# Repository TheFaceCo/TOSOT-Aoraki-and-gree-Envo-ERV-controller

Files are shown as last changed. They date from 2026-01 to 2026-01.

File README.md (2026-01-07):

# TOSOT Aoraki and gree Envo ERV controller
This is a control board for the ductless minisplit ERV manufactured by Gree and sold under the TOSOT brand on amazon et al. It uses an ESP32-S3 WROOM1 microcontroller. 

The ERV is provided with 12V from the minisplit (unknown if this is enabled by default) and accepts PWM speed control. 12V is applied via the 2pin female header. I believe the OEM harness can be jammed onto this header. The ERV pulls about 10W at full speed. 

The motor expects 5V amplitude PWM, so the board includes a small amplifier to step the ESP 3.3v output up to 5v. The PWM output pin is attached to **GPIO1**

There is a standard 0.100" pitch pin header provided for the motor connector. The pitch isn't quite wide enough, but it works. A slightly wider pitch would be better. 

There is a 600mA switching regulator circuit to bring the incoming 12V down to 5v for the PWM, and a subsequent linear regulator to bring 5v down to 3.3v for the ESP32. I am not a SMPS designer, so this was generated using Texas Instruments WBENCH. Two of the ten initial PCB's blew up when power was applied, so this circuit should be considered mildly suspect. The generated assets are included in this repo. 600mA was chosen to allow for the power used by 2x particulate sensors and a CO2 sensor on the 5V rail.

There are two 5-pin JST ZH headers made available to connect Sensirion SPS30 particulate sensors, one for inside and one for outside. These devices are factory configured with identical I2C identifiers and therefore cannot share an I2C bus.  
The ESP32S3 can be configured with two I2C busses. These must be configured as follows:  
    **SDA1: GPIO48**  
    **SCL1: GPIO21**  
    **SDA2: GPIO13**  
    **SCL2: GPIO14**  

Bus #1 is attached to the connector nearest the BOOT and RESET buttons. Bus #2 is attached to the connector on the right-side flag below the power circuitry. 

The SPS30 uses the JST ZH conncetor as well, so a straight-through cable should work correctly. 

There is also a 6pin SH header provided for a Sensirion SCD30 CO2 sensor. This shares I2C bus #2. The SCD30 includes pullup resistors, and this may require that the external pullup resistors on the PCB be removed. This can be done by severing the two exposed traces on the bottom of the board, or by depopulating the two associated pullup resistors. The SCD30 includes a "ready" pin, which is attached to **GPIO12**

Also included is a 3pin JST SH header intended for a potentiometer if that's your preferred input device (If, for example, you intend to use it as a standalone device). 0/3.3V should be applied to the outer two pins, and the wiper should be connected to the center pin. The wiper is attached to **GPIO11**

There is a USB-C connector using the native ESP32 USB pins. This is intended for programming only. It will power the ESP, but not the ERV motor. I did not route the second pair of "B" data pins, so if it doesn't connect to a computer you may need to flip the USB connector. 

If you build firmware with the ESPHome tool in Home Assistant, the following stub should be included in the YAML:

```
fan:  
  - platform: speed  
    output: apartment_erv_fan_pwm  
    name: "Apartment ERV"  

output:  
  - platform: ledc  
    pin:  
      number: GPIO1  
      inverted: False  
      mode:   
        output: True  
        pullup: False  
    id: apartment_erv_fan_pwm  
    inverted: False  
    min_power: 0.20  
    zero_means_zero: True  
```

And the board type selected as follows:

```
esp32:  
  board: esp32-s3-devkitc-1  
  framework:  
    type: esp-idf  
```

PCBA

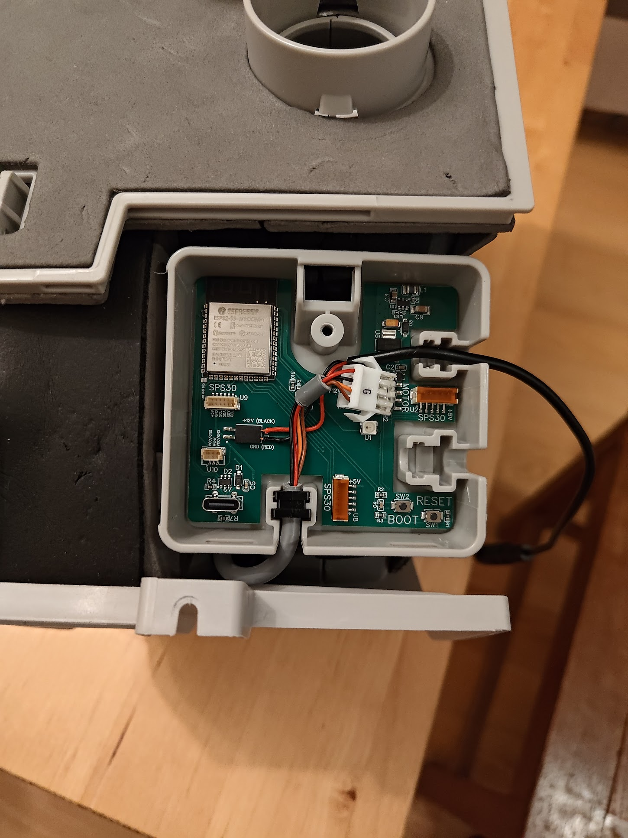
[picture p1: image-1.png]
installed


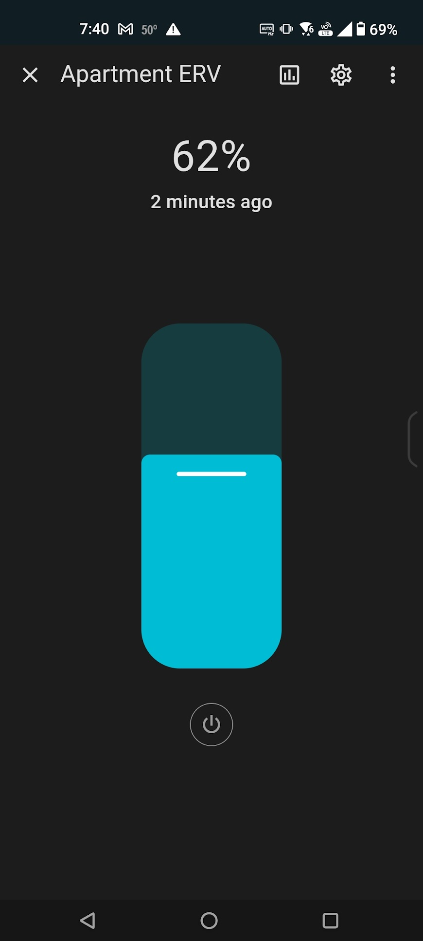
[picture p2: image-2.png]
homeassistant screenshot


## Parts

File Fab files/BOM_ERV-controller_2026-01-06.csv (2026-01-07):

ID | Name | Designator | Footprint | Quantity | Manufacturer Part | Manufacturer | Supplier | Supplier Part | Price | JLCPCB Part Class | link
1 | 10kΩ | R6,R12 | R0402 | 2 | 0402WGF1002TCE | UNI-ROYAL(厚声) | LCSC | C25744 | 0.001 | Basic Part | https://item.szlcsc.com/323315.html
2 | 10uF | C1 | CAP-SMD_L3.2-W1.6-RD-C7171 | 1 | TAJA106K016RNJ | Kyocera AVX | LCSC | C7171 | 0.116 | Basic Part | https://item.szlcsc.com/210648.html
3 | 100nF | C8 | C0402 | 1 | CL05B104KO5NNNC | SAMSUNG(三星) | LCSC | C1525 | 0.001 | Basic Part | https://item.szlcsc.com/15869.html
4 | 47uF | C9 | C1206 | 1 | CL31A476MPHNNNE | SAMSUNG(三星) | LCSC | C96123 | 0.071 | Basic Part | https://item.szlcsc.com/89171.html
5 | TS-1088-AR02016 | SW1,SW2 | SW-SMD_L3.9-W3.0-P4.45 | 2 | TS-1088-AR02016 | XUNPU(讯普) | LCSC | C720477 | 0.045 | Basic Part | https://item.szlcsc.com/457636.html
6 | 22uF | C3 | C0805 | 1 | CL21A226MAQNNNE | SAMSUNG(三星) | LCSC | C45783 | 0.024 | Basic Part | https://item.szlcsc.com/373011.html
7 | B5819W_C8598 | D1,D3 | SOD-123_L2.7-W1.6-LS3.7-RD-1 | 2 | B5819W SL | CJ(江苏长电/长晶) | LCSC | C8598 | 0.023 | Basic Part | https://atta.szlcsc.com/upload/public/pdf/source/20210423/C2828417_EF1BF8BE3D48F97E320B09B073C89160.pdf
8 | 4.7uH | L1 | L1008 | 1 | LQM2HPN4R7MG0L | muRata(村田) | LCSC | C82314 | 0.072 | Extended Part | https://item.szlcsc.com/77923.html
9 | 56.2kΩ | R11 | R0402 | 1 | RC0402FR-0756K2L | YAGEO(国巨) | LCSC | C183355 | 0.001 | Extended Part | https://item.szlcsc.com/323315.html
10 | TPS561208DDCR | U11 | TSOT-23-6_L2.9-W1.6-P0.95-LS2.8-BR | 1 | TPS561208DDCR | TI(德州仪器) | LCSC | C138335 | 0.426 | Extended Part | https://item.szlcsc.com/117832.html
11 | BM06B-SRSS-TB(LF)(SN) | U9 | CONN-SMD-6P-P1.00_BM06B-SRSS-TB-LF-SN | 1 | BM06B-SRSS-TB(LF)(SN) | JST | LCSC | C160392 | 0.311 | Extended Part | https://lcsc.com/product-detail/Wire-To-Board-Wire-To-Wire-Connector_JST-Sales-America_BM06B-SRSS-TB-LF-SN_JST-Sales-America-BM06B-SRSS-TB-LF-SN_C160392.html
12 | BM03B-SRSS-TB(LF)(SN) | U10 | CONN-SMD-3P-P1.00_BM03B-SRSS-TB-LF-SN | 1 | BM03B-SRSS-TB(LF)(SN) | JST | LCSC | C160389 | 0.259 | Extended Part | https://lcsc.com/product-detail/Wire-To-Board-Wire-To-Wire-Connector_JST-Sales-America_BM03B-SRSS-TB-LF-SN_JST-Sales-America-BM03B-SRSS-TB-LF-SN_C160389.html
13 | 10k | R9,R10,R5,R8,R2 | R0603 | 5 |  |  |  |  |  |  | https://www.mouser.in/datasheet/2/447/PYu_RT_1_to_0_01_RoHS_L_11-1669912.pdf
14 | B5B-ZR-SM4-TFT(LF)(SN) | U2,U8 | CONN-SMD_B5B-ZR-SM4-TFT | 2 | B5B-ZR-SM4-TFT(LF)(SN) | JST | LCSC | C471524 | 0.545 | Extended Part | https://static6.arrow.com/aropdfconversion/bba6bb34a80773fcd5c7ec6e0d9cee46c57bd193/ezh.pdf
15 | SK6812MINI-HS | U1 | LED-SMD_4P-L3.5-W3.5-BR_SK6812MINI-HS | 1 | SK6812MINI-HS | 欧思科光电 | LCSC | C2922787 | 0.096 | Extended Part | https://img.jlc.com/pdf/applyPasteComponent/2021-11-17/554769A/a77f6abd580f4801839c6cef98018a08/SK6812MINI-HS.pdf
16 | HX PZ2.0-1X4P WT | H2 | HDR-SMD_4P-P2.00-H-M-W6.0-N | 1 | HX PZ2.0-1x4P WT | hanxia(韩下) | LCSC | C42455215 | 0.065 | Extended Part | https://item.szlcsc.com/993071.html?ref=editor&logined=true
17 | TYPE-C 16P LTH6.8 | U7 | USB-C-SMD_TYPE-C-16P-LTH6.8 | 1 | TYPE-C 16P LTH6.8 | SHOU HAN(首韩) | LCSC | C5187468 | 0.341 | Extended Part | https://atta.szlcsc.com/upload/public/pdf/source/20220929/19C3AE15CC91EF0714EC237D0B90E54B.pdf
18 | 0.1u | C2,C4,C5 | C0603 | 3 |  |  |  |  |  |  | https://item.szlcsc.com/362304.html
19 | SN74LV1T34DCKR | U3 | SC-70-5_L2.1-W1.3-P0.65-LS2.1-BR | 1 | SN74LV1T34DCKR | TI(德州仪器) | LCSC | C78541 | 0.075 | Extended Part | https://atta.szlcsc.com/upload/public/pdf/source/20180404/C202268_2B9476A784C7F34EA71CCBA8021E516C.pdf
20 | HX PM2.0-1X2P WT | U4 | HDR-SMD_HX-PM2.0-1X2P-WT | 1 | HX PM2.0-1x2P WT | hanxia(韩下) | LCSC | C46061752 | 0.142 | Extended Part | https://atta.szlcsc.com/upload/public/pdf/source/20250227/70C7CB114A0F58D1FEED9DC3C611A301.pdf
21 | USBLC6-2SC6_C2687116 | D2 | SOT-23-6_L2.9-W1.6-P0.95-LS2.8-BL | 1 | USBLC6-2SC6 | UMW(友台半导体) | LCSC | C2687116 | 0.038 | Extended Part | https://item.szlcsc.com/169042.html
22 | 100 | R1,R3 | R0603 | 2 |  |  |  |  |  |  | https://www.mouser.in/datasheet/2/447/PYu_RT_1_to_0_01_RoHS_L_11-1669912.pdf
23 | 5.1k | R4,R7 | R0603 | 2 |  |  |  |  |  |  | https://www.mouser.in/datasheet/2/447/PYu_RT_1_to_0_01_RoHS_L_11-1669912.pdf
24 | ESP32-S3-WROOM-1(N8R8) | U5 | WIRELM-SMD_ESP32-S3-WROOM-1 | 1 | ESP32-S3-WROOM-1-N8R8 | ESPRESSIF(乐鑫) | LCSC | C2913201 | 4.911 | Extended Part | https://www.mouser.cn/datasheet/2/891/Espressif_ESP32_S3_WROOM_1_1U_Preliminary-2530171.pdf
25 | AZ1117CH-3.3TRG1 | U6 | SOT-223-3_L6.5-W3.4-P2.30-LS7.0-BR | 1 | AZ1117CH-3.3TRG1 | DIODES(美台) | LCSC | C92102 | 0.076 | Extended Part | https://item.szlcsc.com/410724.html

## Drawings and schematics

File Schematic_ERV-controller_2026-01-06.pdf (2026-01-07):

IO0 27 IO35 28 IO36 29 IO37 30 IO38 31 IO39 32 IO40 33 IO41 34 IO42 35 RXD0 36 TXD0 37 IO2 38 IO1 39 GND 40

## reset

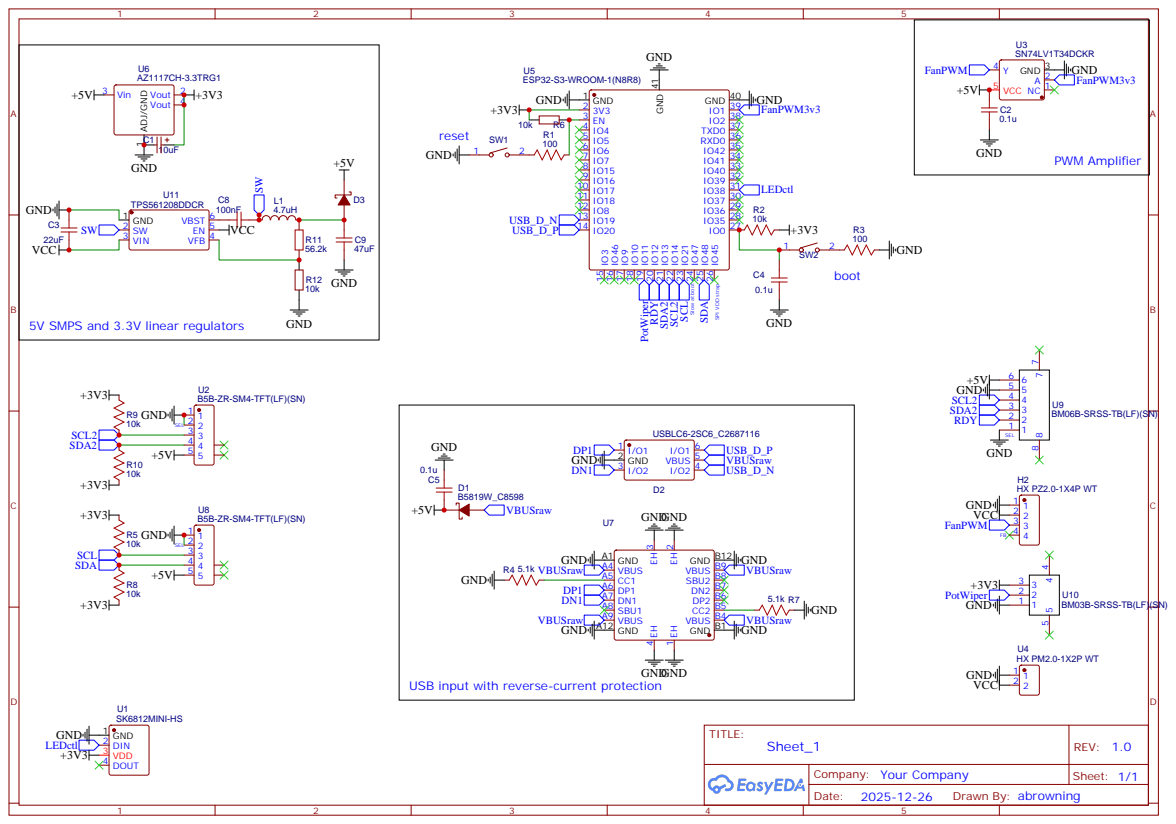
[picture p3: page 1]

5V SMPS and 3.3V linear regulators

USB input with reverse-current protection

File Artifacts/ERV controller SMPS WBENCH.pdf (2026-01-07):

## WEBENCH ® Design Report

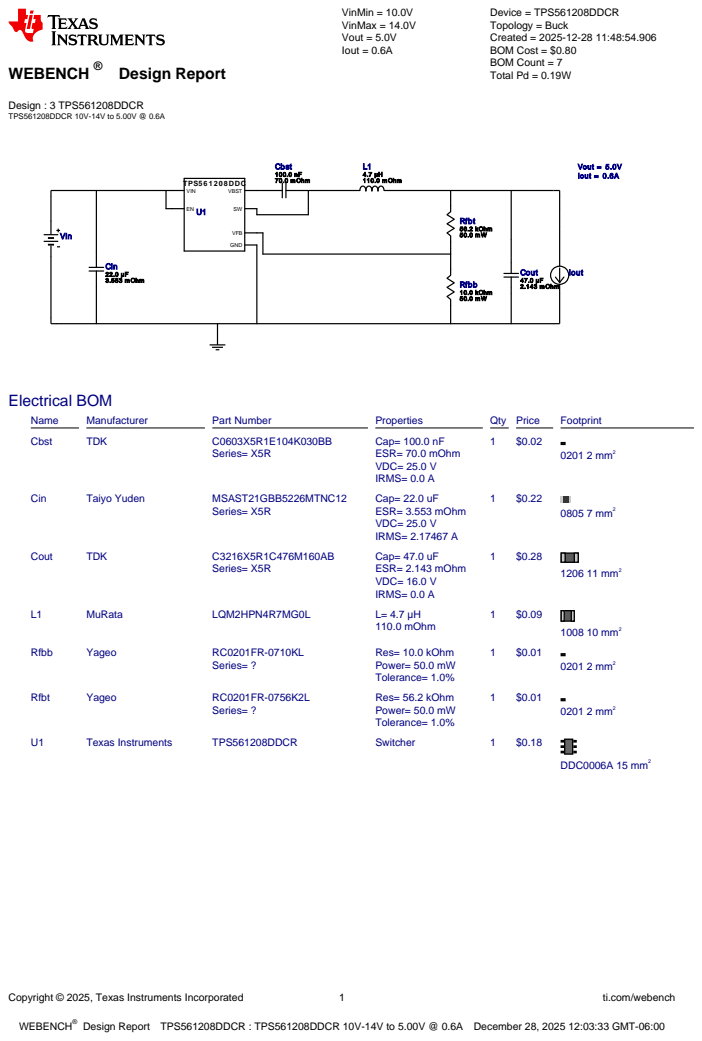
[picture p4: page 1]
Copyright © 2025, Texas Instruments Incorporated; ti.com/webench; WEBENCH®; Design : 3 TPS561208DDCR TPS561208DDCR 10V-14V to 5.00V @ 0.6A; VinMin = 10.0V VinMax = 14.0V Vout = 5.0V Iout = 0.6A; Device = TPS561208DDCR Topology = Buck Created = 2025-12-28 11:48:54.906 BOM Cost = $0.80 BOM Count = 7 Total Pd = 0.19W; Cbst 100.0 nF 70.0 m Ohm; Cin 22.0 µF 3.553 m Ohm; Cout 47.0 µF 2.143 m Ohm; L1 4.7 µH 110.0 m Ohm; Rfbb 10.0 kOhm 50.0 m W; TPS5 6 1 2 0 8 DDC; GND; VIN; VFB; VBST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

Design Report TPS561208DDCR : TPS561208DDCR 10V-14V to 5.00V @ 0.6A December 28, 2025 12:03:33 GMT-06:00

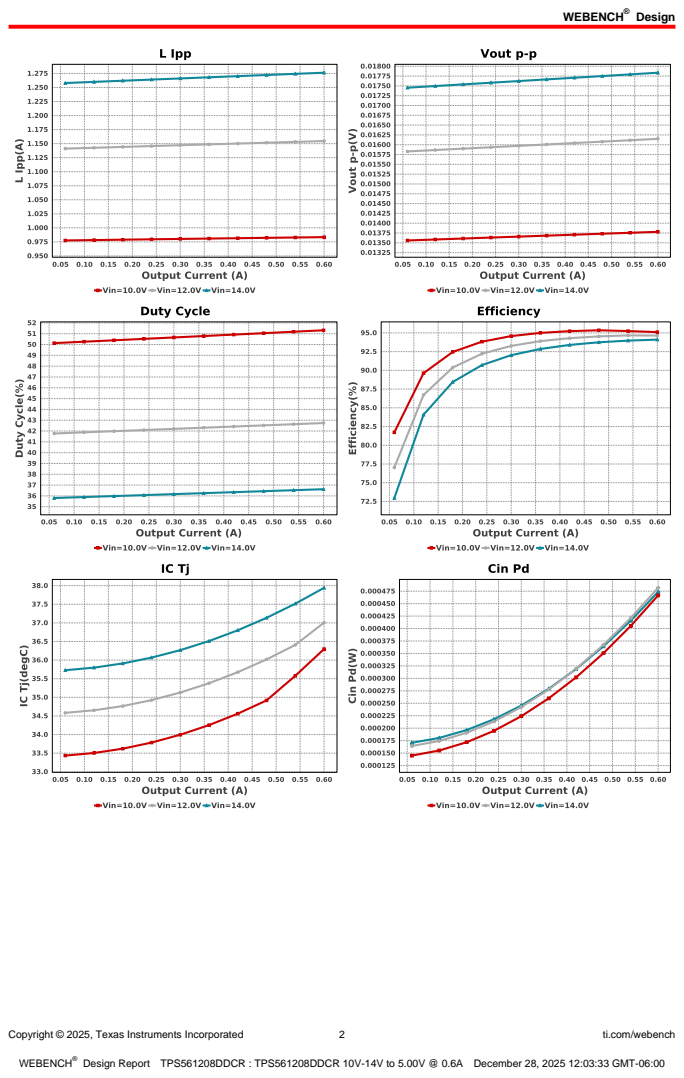
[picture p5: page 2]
Design; Copyright © 2025, Texas Instruments Incorporated; ti.com/webench

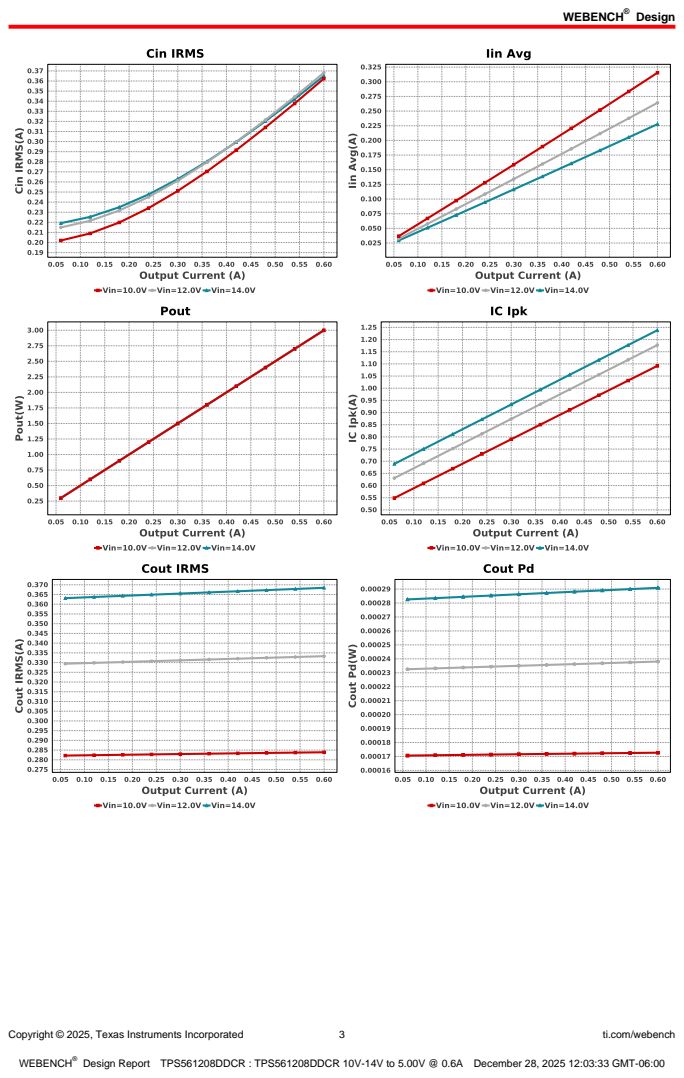
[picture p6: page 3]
Copyright © 2025, Texas Instruments Incorporated; ti.com/webench

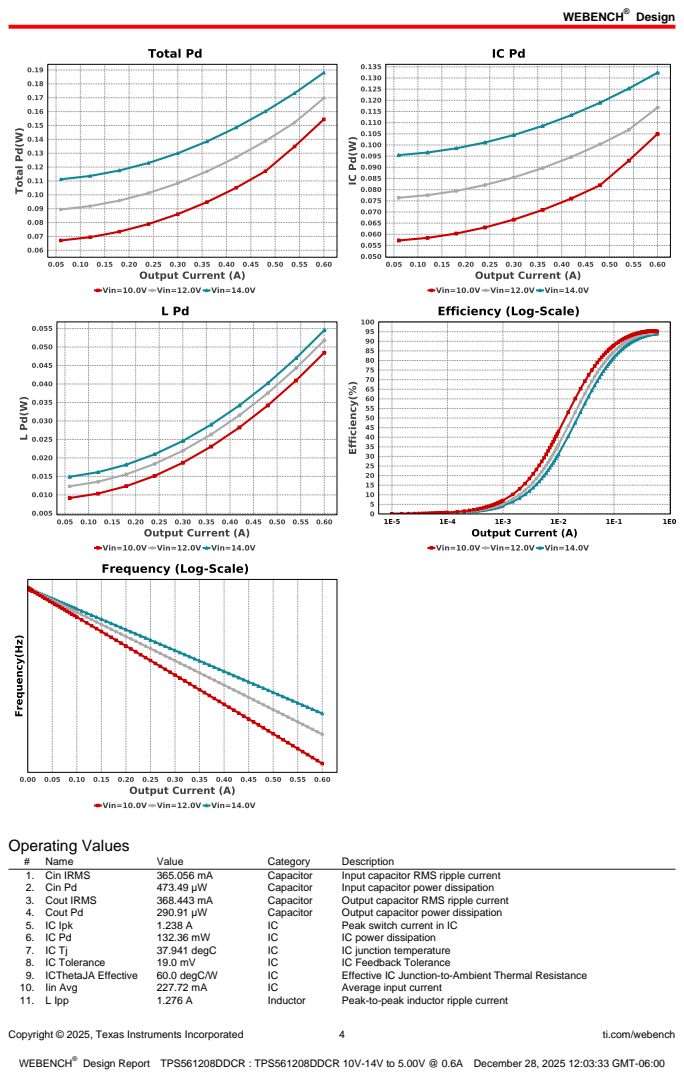
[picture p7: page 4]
Copyright © 2025, Texas Instruments Incorporated; ti.com/webench; Operating Values; Name; Value; Category; Description; 1. Cin IRMS; Capacitor; Input capacitor RMS ripple current; 2. Cin Pd; Input capacitor power dissipation; 3. Cout IRMS; Output capacitor RMS ripple current; 4. Cout Pd; Output capacitor power dissipation; 5. IC Ipk; Peak switch current in IC; IC power dissipation; 37.941 degC; IC junction temperature; 8. IC Tolerance; IC Feedback Tolerance; 9. ICThetaJA Effective; 60.0 degC/W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

Copyright © 2025, Texas Instruments Incorporated | 5 | ti.com/webench
# | Name | Value | Category | Description

12. L Pd | 54.533 mW | Inductor | Inductor power dissipation
13. Cin Pd | 473.49 µW | Power | Input capacitor power dissipation
14. Cout Pd | 290.91 µW | Power | Output capacitor power dissipation
15. IC Pd | 132.36 mW | Power | IC power dissipation
16. L Pd | 54.533 mW | Power | Inductor power dissipation
17. Total Pd | 188.033 mW | Power | Total Power Dissipation
18. BOM Count | 7 | System
| | | Information | Total Design BOM count
19. Duty Cycle | 36.619 % | System
| | | Information | Duty cycle
20. Efficiency | 94.102 % | System
| | | Information | Steady state efficiency
21. FootPrint | 49.0 mm² | System
| | | Information | Total Foot Print Area of BOM components
22. Frequency | 540.168 kHz | System
| | | Information | Switching frequency
23. Iout | 600.0 mA | System
| | | Information | Iout operating point
24. Mode | FCCM | System
| | | Information | Conduction Mode
25. Pout | 3.0 W | System
| | | Information | Total output power
26. Total BOM | $0.8 | System
| | | Information | Total BOM Cost
27. Vin | 14.0 V | System
| | | Information | Vin operating point
28. Vout | 5.0 V | System
| | | Information | Operational Output Voltage
29. Vout Actual | 5.084 V | System
| | | Information | Vout Actual calculated based on selected voltage divider resistors
30. Vout Tolerance | 4.231 % | System
| | | Information | Vout Tolerance based on IC Tolerance (no load) and voltage divider resistors if applicable
31. Vout p-p | 17.836 mV | System
| | | Information | Peak-to-peak output ripple voltage

## Design Inputs

Name | Value | Description
| Iout | | 600.0 m | Maximum Output Current
VinMax | 14.0 | Maximum input voltage
VinMin | 10.0 | Minimum input voltage
Vout | 5.0 | Output Voltage
| base_pn | | TPS561208 | Base Product Number
source | DC | Input Source Type
Ta | 30.0 | Ambient temperature


Copyright © 2025, Texas Instruments Incorporated | 6 | ti.com/webench

## Assembly

## Component Testing

Some published data on components in datasheets such as Capacitor ESR and Inductor DC resistance is based on conservative values that will guarantee that the components always exceed the specification. For design purposes it is usually better to work with typical values. Since this data is not always available it is a good practice to measure the Capacitance and ESR values of Cin and Cout, and the inductance and DC resistance of L1 before assembly of the board. Any large discrepancies in values should be electrically simulated in WEBENCH to check for instabilities and thermally simulated in WebTHERM to make sure critical temperatures are not exceeded.
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

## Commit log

2026-01-07 publish
    originate
    [BOM_ERV-controller_2026-01-06.csv, PickAndPlace_PCB_ERV-controller_2026-01-06.csv]
2026-01-07 add design docs
    [PCB_ERV-controller_2026-01-07.pcbdoc, Sheet_1_2026-01-07.schdoc]

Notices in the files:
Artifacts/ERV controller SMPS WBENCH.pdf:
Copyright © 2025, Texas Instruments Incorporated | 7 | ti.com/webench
